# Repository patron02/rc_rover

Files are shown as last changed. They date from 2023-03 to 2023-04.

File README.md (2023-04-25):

# RC Rover

The goal of this project is to create an efficient H-bridge circuit that can be used for motor control in various scenarios. The H-bridge circuit is a crucial component in robotics, and this project aims to demonstrate its functionality by building a rover test platform. The primary objective is to design a circuit that allows the rover to move in different directions, such as forward, backward, left, and right, while maintaining stability and control.

The H-bridge circuit will have multiple applications in robotics and other industries, such as automotive and aerospace. It can be used to control motors in robots, drones, electric vehicles, and many other devices. By creating a robust and efficient H-bridge circuit, this project aims to contribute to the advancement of motor control technology.

The rover test platform will showcase the H-bridge circuit's capabilities in a real-world scenario. The platform will be able to traverse different terrains, navigate obstacles, and perform various maneuvers, demonstrating the circuit's stability and reliability. Overall, this project aims to provide a practical learning experience in motor control and robotics while contributing to the development of efficient motor control technology for various industries.

# Meeting 1:

Date: 03/12/23
Time: 9:15 - 12 PM

Reference Material: https://ecetechprojects.wordpress.com/2011/07/08/arduino-h-bridge-motor-control/

Finalized Proposal: https://1drv.ms/w/s!At5nmv7gLyVwkvE4l1jkQC4PCUBfSg?e=4K8k71

Discussed the H-Bridge Design and decided which parts would be used
  - Decided on using PNP and NPN transistors
  - 9V battery
  - DC motors
  
Sketched a simple reference circuit and built it for testing. While this circuit works, we found it to be lackluster in performance.
 
 

# Meeting 2:

Date: 03/18/23
Time: 2 - 8 PM

We made a simple schematic with transistors to understand the basics of how it would all work. We then decided to change the circuit to mosfets because VCC is higher than the gate voltages and because the mosfets have built-in reverse-bias diodes to help with overvoltage spikes when the car is braking. After we did that, we realized we still needed an NPN transistor to control the mosfets. The new circuit has 4 mosfets and 2 transistors. We used 10kohm pull-up resistors on the P-channel gates to latch them shut. According to our math this means we'll have ~0.1mA through the transistors. This will affect which resistor we put on the transistors bases. For now it's 2.2k but we might need to increase that a bit to 10k as well for less current on the base.

Using a 10k resistor  in series with the 2N2222 Collector, we will see around 1mA, assuming 10V from the battery. Using a 2.2k resistor in series with the 2N2222 Base, we see 1.4mA, assuming 3.0v from the Pi. Given these parameters, we will expect <0.1V from the collector to emitter, so the MOSFET Gates will be basically grounded when the respective PI pin is HIGH. Conversely, in order flip the MOSFET gates HIGH, current into the base will need to be <7nA. Assuming we're using the 2.2k resistor, the PI output pin must be at <0.0154V relative to ground. In the real world, this might prove difficult, and testing will be required.



Updated TinkerCad:



Parts List: https://1drv.ms/x/s!At5nmv7gLyVwkvcxxzeMtASVYCzkrQ?e=bIrlzk

# Meeting 3:

Date: 03/19/23
Time: 5 - 9 PM

Reference Material: https://datasheets.raspberrypi.com/rpi3/raspberry-pi-3-b-plus-reduced-schematics.pdf

We designed a simple chassis and printed it. As for the power system we are using a 9.6V 2000 mAh battery with a voltage regulator for the H bridge circuit and a voltage regulator to power the pi with 5V. The remaining parts were also bought. 



 

# Meeting 4:

Date: 03/24/23
Time: 12-12:30 PM
 
We are waiting for the remaining parts to arrive in the mail. 1/4 motors is completely built and tested. All that is left is building the full circuit on the breadboard and running tests on it. We spoke to Dr.Wolfe and discussed possibly presenting our demo earlier than the proposed presentation date. 

 

# Meeting 5:

Date: 03/25/23
Time: 6-9 PM

Reference Material: https://github.com/besp9510/dma_pwm

We were choosing between running the motors with a constant DC source and changing the voltage in order to change the speed or using PWM. With DC we could only get down to 4 [V]. With PWM, it went as low as 1.5vRMS and was still turning, and it is much easier to code. We ran some tests on the circuit with a frequency generator to test the PWM and saw some 1 [A] spikes from each motor. We discussed adding a filter or switching the motors so they are staggered so that we don't blow a fuse in our circuit. 



An example of what we could do to stagger the motors:



We finished fully building the rover, the only thing remaining was adding all the connectors and the circuit.

   

We discussed which controller we would use to control the robot. We could connect an Xbox controller with analog thumb sticks using bluetooth or use a numpad with different numbers signalling different speeds. We need to work on the code so we can program the directions using the following table:
 
 

We also finalized a simple schematic for how the switchboard will be wired up suppling VCC to the voltage regulator, RPI regulator and light



Current version of the H-Bridge schematic:

 

# Meeting 6:

Date: 03/30/23
Time: 2:30 - 5 PM

Reference Material: https://learn.adafruit.com/improve-brushed-dc-motor-performance/pwm-and-brushed-dc-motors

Finalized Working TinkedCad Circuit: https://www.tinkercad.com/things/bnNonHPksck-fantastic-hillar/editel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

PWM Motor Calculations: https://1drv.ms/x/s!At5nmv7gLyVwkvc0S1sMwEzTU4Yw9A?e=w484rG

The rover circuit was built on a separate breadboard for testing and we got 1 wheel working. We will eventually build the circuit on the breadboard that is already attached to the rover. The flyback diode in the circuit and the mosfets fixed the spikes that appeared when using PWM. Most of the code was written and added to the github repository. 

 

Finalized circuit schematic:



# Meeting 7: 

Date: 04/08/23
Time: 4-6 PM

Reference Material: https://github.com/zeth/inputs

The circuit was fully built and tested. We had a small setbacks with a regulator breaking but a new one was ordered to replace the broken one. Currently the rover is being controlled by a keypad but we are working on converting that to a joystick so that it is easier to work with. 

  

The joystick will output a rectangular coordinate which needs to be converted to polar coordinates. Polar coordinates are typically used for omniwheels because their direction is controlled through angles which can be more intuitively visualized through polar coordinates. We will then add 315 to the polar angle to get rid of the negative angles for when the rover moves backwards. Then we can use the function dif['angle'] %= 360 to convert to 0~360 degrees. Then take cos() and sin() to get speed for the wheels and multiply each speed by the polar magnitude. That will give us the PWM duty cycle for each wheel. If it's positive, it will be put on pins 13, 9, 25, and 20. If it's negative (the wheel is going backwards) so it will be put on the output pins 26, 11, 16 and 21.

  

# Final Images:



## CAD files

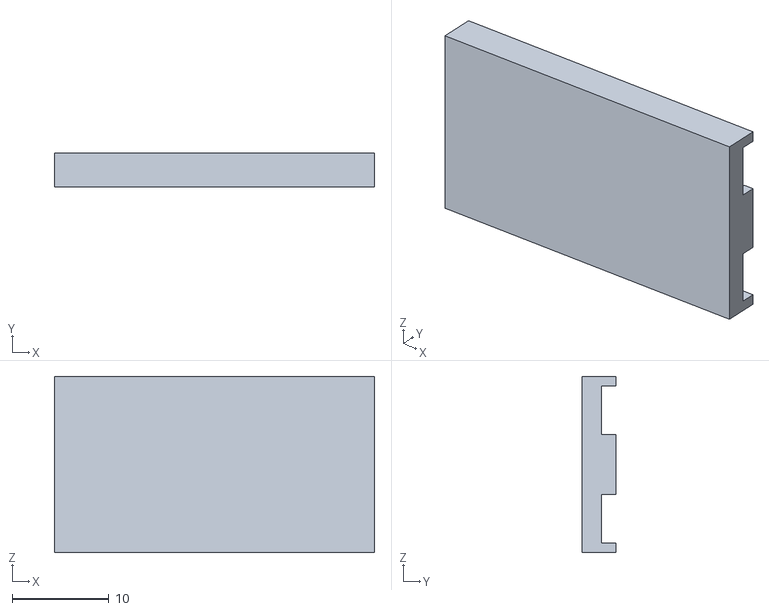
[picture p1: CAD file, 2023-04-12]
3D_Files/dc-dc_holder_RPI.stl
33.0 x 3.50 x 18.2

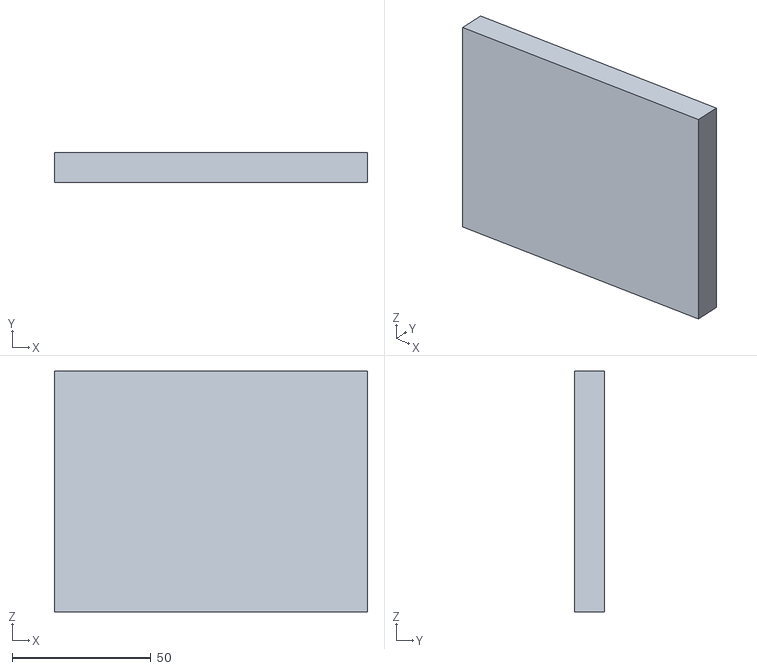
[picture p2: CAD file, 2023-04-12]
3D_Files/breadboard holder.stl
113.0 x 11.0 x 87.0

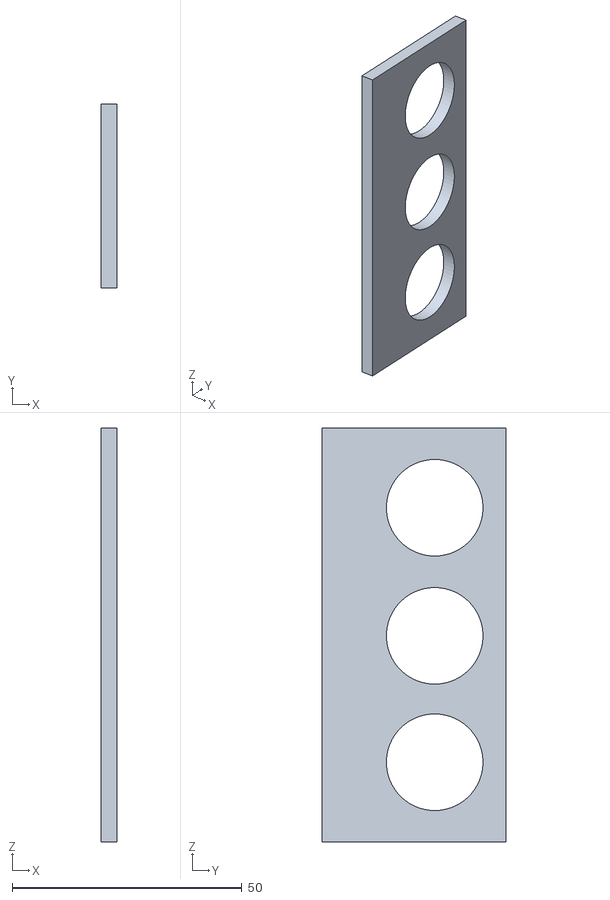
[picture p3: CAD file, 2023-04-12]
3D_Files/switchpanel.stl
3.54 x 40.0 x 90.0

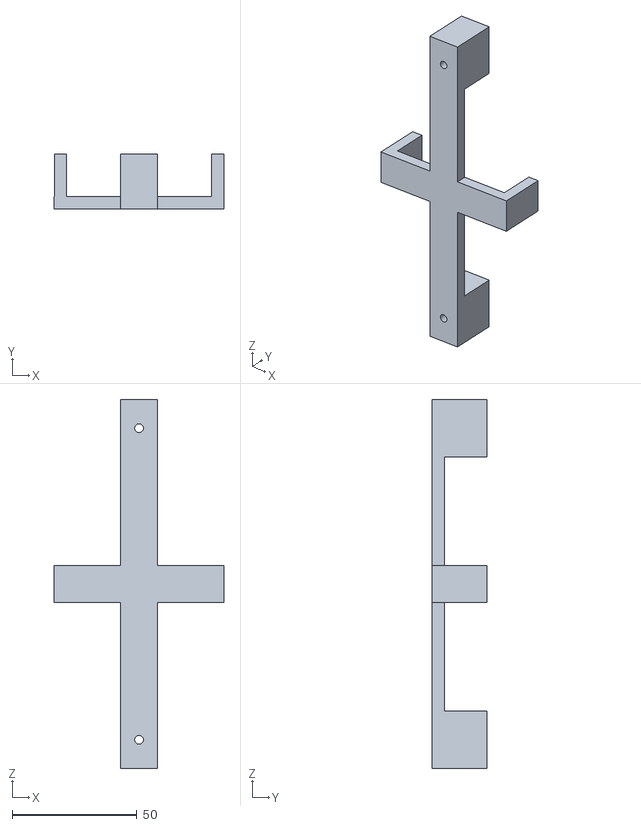
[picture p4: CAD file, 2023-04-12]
3D_Files/battery holder.stl
68.0 x 22.0 x 148.0

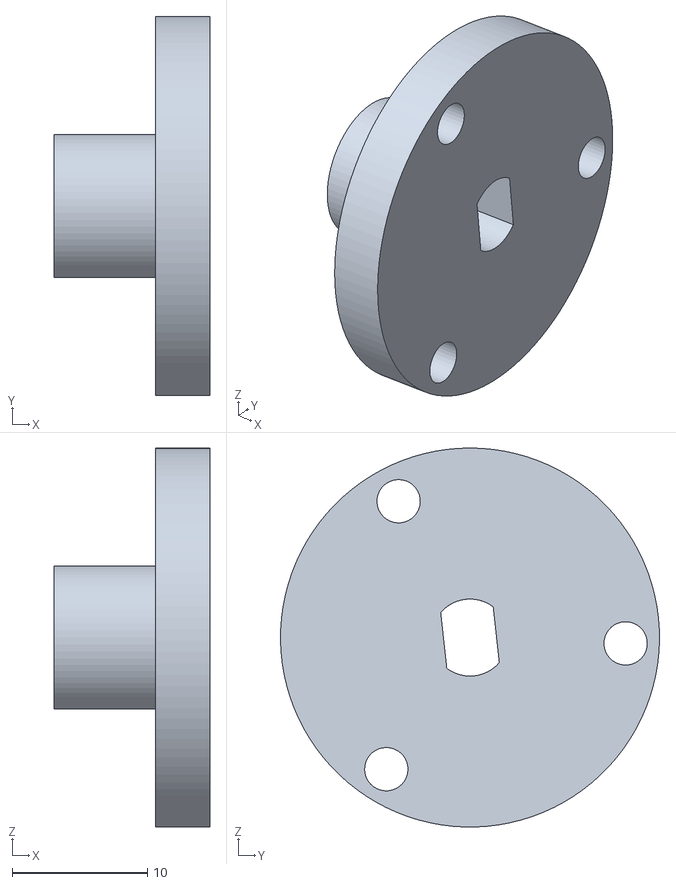
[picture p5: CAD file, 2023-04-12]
3D_Files/motor hub.stl
11.5 x 28.0 x 28.0

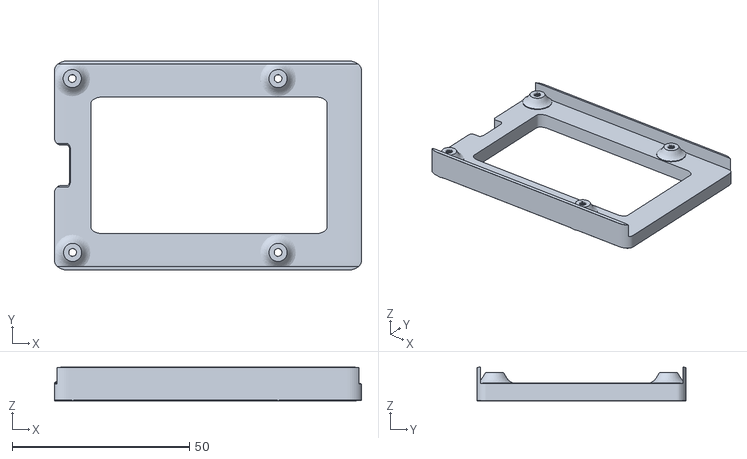
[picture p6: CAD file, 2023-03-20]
3D_Files/RPI_Holder.stl
86.5 x 59.0 x 9.54

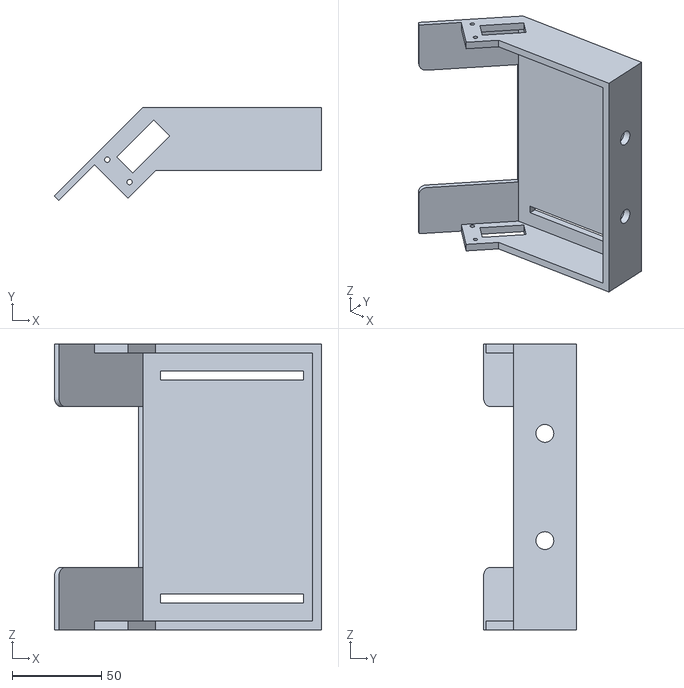
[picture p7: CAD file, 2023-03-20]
3D_Files/Rover_Body.stl
149.5 x 52.0 x 160.0

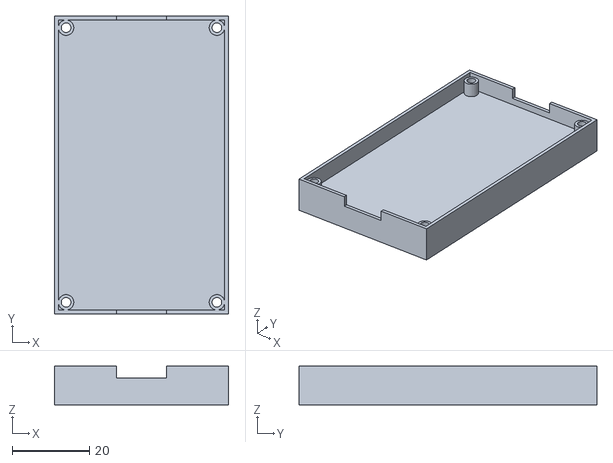
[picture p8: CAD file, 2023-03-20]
3D_Files/Drok_DC-DC_holder.stl
45.0 x 77.0 x 10.0

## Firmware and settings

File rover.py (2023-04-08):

import tkinter as tk
import RPi.GPIO as gpio

# Motor Connections on Pi
# motor M1: pins 20 and 21  (Back Right)
# motor M2: pins 13 and 26  (Back Left)
# motor M3: pins 25 and 16   (Front Right)
# motor M4: pins 9 and 11   (Front Left)

# Define pin mapping using a dictionary
pin_mapping = {
    'w': [9, 13, 20, 25],  # Forward \
    's': [11, 16, 21, 26],  # Back \
    'a': [11, 13, 21, 25],  # Left \
    'd': [9, 16, 20, 26],  # Right \
    
    'e': [9, 20],  # Forward Right \
    'z': [11, 21],  # Back Left \
    'q': [13, 25],  # Forward Left \
    'c': [16, 26],  # Back Right \
    
    ']': [9, 13, 16, 21],  # Rotate Right \
    '[': [11, 20, 25, 26],  # Rotate Left \
}

# Setup pins as outputs
gpio.setmode(gpio.BCM)
for pins in pin_mapping.values():
    for pin in pins:
        gpio.setup(pin, gpio.OUT) #defines all listed pins as Outputs
        gpio.output(pin, gpio.LOW) #set all pins LOW by default

pin = [] # initialize pin variable

def press_key(event):
    global pin # use the global pin variable
    key = event.char.lower() # get the pressed key in lowercase
    pin = pin_mapping.get(key, []) # get the corresponding pins for the key
    for p in pin:
        gpio.output(p, gpio.HIGH) # set each pin high

def release_key(event):
    global pin # use the global pin variable
    for p in pin:
        gpio.output(p, gpio.LOW) # set each pin low

root = tk.Tk()
root.bind('<KeyPress>', press_key)
root.bind('<KeyRelease>', release_key)
root.mainloop()

gpio.cleanup()
